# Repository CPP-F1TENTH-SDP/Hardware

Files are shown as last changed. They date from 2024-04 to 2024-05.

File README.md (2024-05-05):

# Cal Poly Pomona F1TENTH Project: Hardware Files and Documentation 
Welcome to Cal Poly Pomona's F1TENTH SDP Group. Here is where we posted any hardware files and documentation that were used throughout the project. The hardware was based on a modified list of items that the official F1Tenth website has 
[layed out](https://f1tenth.org/build.html). 

For setting up and using the Jetson Nano (including getting Docker and ROS2 setup) [Click Here!](https://github.com/CPP-F1TENTH-SDP/Hardware/wiki)

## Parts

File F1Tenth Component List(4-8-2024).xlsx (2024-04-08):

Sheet: Main Page
 | Qty | Cost per unit | Total Cost (USD) | Comments | Location (Some can be bought in-person) | Link
Chassis
Traxxxas Slash 4x4 Platinum Editon | 1 | 399.99 | 399.99 | don't need to replace motor and comes with tsm |  | https://www.rcsuperstore.com/traxxas-slash-4x4-vxl-brushless-rtr-short-course-rc-truck-w-tsm/?sku=TRA68086-4-VISN
(Alternative) Lipos Battery | 1 | 69.95 | 69.95 |  |  | https://traxxas.com/products/parts/batteries/idpowercellbatteries/lipo/2832X-5000mah-111v-3S-25C
(Alternative) charger/battery combo | 1 | 119.95 | 119.95 |  |  | https://traxxas.com/products/parts/2970-3S
Antenna Mount (3D print) | 1 | 0 | 0 | Can use makers studio |  | https://drive.google.com/drive/u/0/folders/1o_TlCaeVCjFml82t8zExDaT-06q3OWqf
Platform Deck (lasercut) | 1 | 2.99 | 2.99 | use lasercutter in makers studio |  | https://www.amazon.com/ABS-Sheet-Thick-Black-Nominal/dp/B004UBUX5C
Fasteners |  |  | 0
M3 Socket Head Kit | 1 | 9.88 | 9.88 |  |  | https://www.amazon.com/iExcell-Stainless-Socket-Screws-Assortment/dp/B07CXKDJ7X?s=industrial
M5 Socket Head Kit | 1 | 8.26 | 8.26 |  |  | https://www.amazon.com/iExcell-Stainless-Socket-Screws-Assortment/dp/B07SBQ1JX5?s=industrial
6mm hex 14mm M3 standoffs | 2 | 3.93 | 7.86 |  |  | https://www.mcmaster.com/94868A009/
6mm hex 25mm M3 standoffs | 4 | 5.75 | 23 |  |  | https://www.mcmaster.com/94868A013/
6mm hex 45mm M3 standoffs | 6 | 4.31 | 25.86 |  |  | https://www.mcmaster.com/94868A190/
M2.5 x 0.45mm, 6mm long | 1 | 6.14 | 6.14 | Pack of 50, used with .12" platform deck |  | https://www.mcmaster.com/94500A213/
M2.5 x 0.45mm, 10mm long FF Standoffs | 4 | 0.73 | 2.92 |  |  | https://www.mcmaster.com/95947A005/
Compute Module |  |  | 0
~~Jetson Xavier NX~~ | ~~1~~ | ~~0~~ | ~~0~~ | Obsolete by both the Orin Nano and the Orin NX
(Alt) Jetson Orin NX (8gb) | 1 | 659 | 659 | There's a third-party dev board that features a Orin NX (8gb) model. (Future Model if necessary) |  | https://www.waveshare.com/jetson-orin-nx-16g-dev-kit.htm?sku=24474
(Alt 2) Jetson Orin Nano (8gb) | 1 | 499 | 499 | This is also a more powerful version of the Xavier NX and it's cheaper. However it lacks some AI learning features. |  | https://store.nvidia.com/en-us/jetson/store/?page=1&limit=9&locale=en-us
Micro SD Card (32GB or More) | 1 | 12.99 | 12.99 |  |  | https://www.amazon.com/SanDisk-Extreme-microSDXC-Memory-Adapter/dp/B09X7BK27V?s=electronics
(Optional) NVME SSD (250gb or More) | 1 | $39.99 | 39.99 |  |  | https://www.amazon.com/dp/B0BRQTMX1N?tag=pcpapi-20&linkCode=ogi&th=1
Sensors |  |  | 0
Electronics |  |  | 0
VESC 6 MkV | 1 | 290.25 | 290.25 |  |  | https://trampaboards.com/vesc-6-mkvi-the-amazing-trampa-vesc-6-mkvi--gives-maximum-power-original-p-27536.html
LiPo safety bag like the Aketek Silver Large Size Lipo Battery Guard Sleeve/Bag for Charge & Storage. | 2 | 9.99 | 19.98 |  |  | https://www.amazon.com/Fireproof-Battery-Drone-Storage-Silver/dp/B07KVZYRJ9?s=hi
Barrel Jack to Pigtail | 1 | 4.97 | 4.97 |  |  | https://www.digikey.com/en/products/detail/tensility-international-corp/10-01779/5638255
12V 5A Power Adapter (optional) | 1 | 11.99 | 11.99 |  |  | https://www.amazon.com/Adapter-100-220V-Switching-Security-Accessories/dp/B0711Q5B49?link_code=qs
Antenna | 1 | 13.99 | 13.99 |  |  | https://www.amazon.com/dp/B0BD3WSQFD?s=pc&sp_csd=d2lkZ2V0TmFtZT1zcF9kZXRhaWw
Intel RealSense D345i | 1 | 334 | 334 |  |  | https://store.intelrealsense.com/buy-intel-realsense-depth-camera-d435i.html
Miscellaneous |  |  | 0
TRX to XT90 Adapter | 1 | 10.99 | 10.99 |  |  | https://www.amazon.com/dp/B07QMJ8XGF
Traxxas id charge lead adapter | 1 | 5.99 | 5.99 |  |  | https://www.progressiverc.com/products/trx-id-connector-converter?variant=34490791919751
Header Pins | 1 | 8.99 | 8.99 |  |  | https://www.amazon.com/DIKAVS-Break-Headers-Header-Connector/dp/B076F64ZCJ?link_code=qs
VESC ppm cable | 1 | 6.95 | 6.95 |  |  | https://www.ollinboardcompany.com/product/vesc6-ppm-connector
HDMI emulator | 1 | 8.5 | 8.5 |  |  | https://www.amazon.com/CompuLab-fit-Headless-Display-Emulator/dp/B00FLZXGJ6
short (~1 ft) A USB-to-microUSB cable | 1 | 8.99 | 8.99 |  |  | https://www.amazon.com/Sabrent-6-Pack-Premium-Cables-CB-UM61/dp/B011KMSNXM?s=Industrial%2B%26%2BScientific
Bullet Adapter 4mm Male 3.5mm Female | 1 | 10.15 | 10.15 |  |  | https://www.amazon.com/Great-Planes-Female-Bullet-Adapter/dp/B001C34TC4
Total: |  |  | 2623.52
For Later
Xbox Controller | 1 | 22.99 |  |  |  | https://www.amazon.com/Wireless-Controller-Compatible-Joystick-Receiver/dp/B09WQGQ6D2?s=electronics
3500 kv Brushless Motor | 1 | 89.95 |  |  |  | https://www.amazon.com/Traxxas-Velineon-Brushless-Motor-3500Kv/dp/B00XWTXOCC
Hokuyo 10LX | 1 | 1670 |  |  |  | https://acroname.com/store/scanning-laser-rangefinder-ethernet-r359-ust-10lx

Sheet: PowerBoard
Comment | Quantity | Cost |  | Components | Digikey Part Number | Order Link | Comment
Power Board | 1 | $30.00 | $30.00 |  |  | https://tinyurl.com/f110powerboard2019 | Comes in packs of 3
560 ohm | 1 | $0.10 | $0.10 | R1 | ‎CF14JT560RCT-ND‎ (https://www.digikey.com/product-detail/en/CF14JT560R/CF14JT560RCT-ND/1830344/?itemSeq=302805132) |  | Any resistor around 500 ohm should work
0.33uF | 1 | $0.56 | $0.56 | C5 | ‎445-181227-1-ND‎ (https://www.digikey.com/product-detail/en/FG16X7R2A334KNT06/445-181227-1-ND/9740707/?itemSeq=302805131) |  | CAPACITOR, American symbol
0.1uF | 3 | $0.23 | $0.69 | C6, C3, C4 | BC1084CT-ND |  | CAPACITOR, American symbol
100uF | 2 | $0.40 | $0.80 | C1, C2 | ‎P5182-ND‎ (https://www.digikey.com/product-detail/en/ECA-1HM101/P5182-ND/245041/?itemSeq=302805123) |  | CAPACITOR, American symbol
10uF | 1 | $0.25 | $0.25 | C7 | 493-5915-1-ND‎ (https://www.digikey.com/product-detail/en/UVR1H100MDD1TD/493-5915-1-ND/3438479/?itemSeq=302805129) |  | CAPACITOR, American symbol
12V to 8V LDO | 1 | $0.86 | $0.86 | U1 | BA7808CP-E2CT-ND‎ (https://www.digikey.com/product-detail/en/BA7808CP-E2/BA7808CP-E2CT-ND/2357332/?itemSeq=302805130) |  | 12V to 8V LDO
12V_TRANSFORMER | 1 | $42.91 | $42.91 | U$9 | ‎102-3892-ND‎ (https://www.digikey.com/product-detail/en/PDQ30-Q24-S12-D/102-3892-ND/6165425/?itemSeq=302805124) |  | CUI Inc ?? SERIES: PDQ30-D ?? DESCRIPTION: DC-DC CONVERTER http://www.mouser.com/pdfdocs/pdq30-d.pdf
2 Pin Terminal Blocks | 7 | $1.08 | $7.56 | X1, X2, X3, X4, X5, X6, X7 | ‎ED10561-ND‎ (https://www.digikey.com/product-detail/en/OSTVN02A150/ED10561-ND/1588862/?itemSeq=302805120) |  | .100 (2.54mm) Center Header - 2 Pin"
Toggle Switch | 1 | $4.41 | $4.41 | U$3 | ‎360-3240-ND‎ (https://www.digikey.com/product-detail/en/M2011S2A1W01/360-3240-ND/1049342/?itemSeq=302805119) |  | SPST two lead switch Pin 2 is common Swtich Closed on Down Position DigiKey: http://www.digikey.com/product-detail/en/nkk-switches/M2011S2A1W01/360-3240-ND/1049342 Data Sheet: http://2t70un3m1d9z1kztamkdrd38.wpengine.netdna-cdn.com/wp-content/uploads/2016/02/MtogglesBushing.pdf
4 Pin Connector | 1 | $0.22 | $0.22 | U$10 | 455-2249-ND‎ (https://www.digikey.com/product-detail/en/B4B-XH-A(LF)(SN)/455-2249-ND/1651047/?itemSeq=302805122)
Power LED | 1 | $0.14 | $0.14 | LED 1 | 2368-NTE3146-ND |  | LED power indicator, Or any other 5mm LED, current around 20 mA, Or any other 5mm LED, current around 20 mA
 |  |  | $88.50

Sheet: Tools
 | Cost | Qty. | Comments | Link
Tools
Metric ruler |  | 1
Needle-nose pliers |  | 1
2mm width or smaller flathead screwdriver |  | 1
screwdriver set |  | 1
adjustable wrench (to hold standoffs in place) |  | 1
T3 Torx screwdriver |  | 1 | used to remove TX2
Wireless router |  | 1
Double Sided Tape |  | 1 | (for mounting USB hubs and optionally VESC)
Track Material
Air Duct Material (for creating a race Track) |  | - |  | https://www.amazon.com/Hon-Guan-inch-Air-Duct/dp/B07VRMPSLG/
Laser cut the mounts |  | - |  | https://drive.google.com/drive/folders/1nt0ZO4beQ2dVvx_JtG515-q1HvWNrgP5?usp=sharing
Video Material for set up the track |  | - |  | https://www.dropbox.com/s/z07opm0f2e17y7y/F1-10%20pop-up%20racetrack.mp4?dl=0 and https://www.dropbox.com/s/ludl84vr90nupwc/10%20live%20demo%20.mp4?dl=0
Peripherals
USB keyboard and mouse |  | 1
HDMI display |  | 1
HDMI-to-HDMI cable (to connect car to display) |  | 1
Ethernet cable |  | 1
Extras
RC Car Jack | 11.97 | 1 |  | https://www.amazon.com/Hobbypark-Aluminum-Workstation-Rotation-Buggies/dp/B079P3P8FN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

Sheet: Update Log
9/10/23: Initial Excel Sheet created
9/11/23: Added Intital Components
9/11/23: Made the excel file editable.
9/12/23: Added the 2nd Shopping List. This will be our main list.
9/13/23: Added new micro SD card link that has more storage with a slightly lower price.
Some comments are added for the Jetson, the NVMe SSD, and for the 3D printing in the Main Page
9/18/23: Cross off the Hokuyo scanner off the list
Made NVMe optional
We'll be using the Slash
We'll have to decide on what Nvidia Jetson model do we want.
The power adapter is optional.
Made a new "For Later" list for components that will have to be bought at another time.
Tools and PowerBoard tabs are also created
9/25/23:
~~Xavier NX is obsolete by the Orin NX and the Orin Nano. Please choose either one of those two newer options, unless otherwise. ~~
Updated Prices on SSD
Shorten (Alternative) on the two alternative Jetson models
The Secondary Page WILL BE DELETED BY NEXT WEEK ON 10/2/23
Main Page recieves some design revamps, and minor spelling and grammar adjustments.
Orin NX will likely be our computer module of choice.
2023-10-02
Deleted the Secondary Page as promised
2024-04-08
Updated some of information. Key additions include:
1. Readded the Hokuyo LiDAR scanner on the list.
2. Added the Traxxas ID Charge Lead Adapter on the list.
3. Hyperlinked the Intel Realsense link

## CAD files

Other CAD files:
Platform_Deck/Platform_Deck_V4.x_t

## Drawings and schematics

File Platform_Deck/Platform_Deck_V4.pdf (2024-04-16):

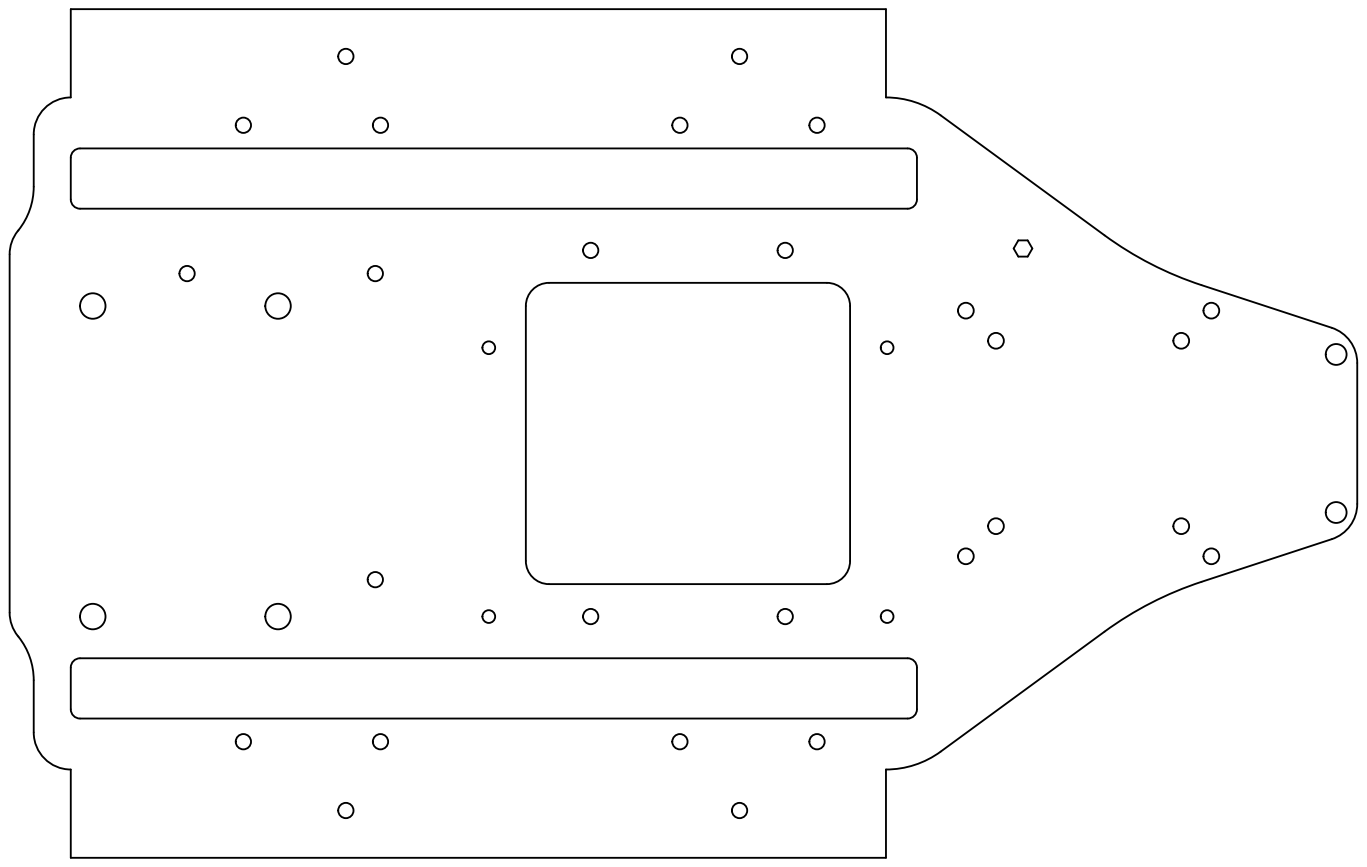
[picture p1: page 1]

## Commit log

2024-04-16 Add files via upload
    PowerBoard Schematics for the version 4 board with a modification adjust the 8V output down to 5V
    [PowerBoard_V1.kicad_pcb, PowerBoard_V4.1_5VOutput.kicad_sch]
2024-04-16 Add files via upload
    Updated the Platform deck to mount to the new version of the Traxxxas Slash 4x4 Platinum Editon.
    Removed the antenna mount.
    [Platform_Deck_V4.x_t]
